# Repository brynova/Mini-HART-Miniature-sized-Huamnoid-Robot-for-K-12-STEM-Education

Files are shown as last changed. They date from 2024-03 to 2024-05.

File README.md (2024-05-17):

# Mini-HART 
The goal of this project is to create an affordable humanoid robot that will be used as an educational tool in the classroom. This humanoid can teach 9-12th grade students several aspects of STEM through its creation and use. These aspects consist of items such as 3-D modeling, design, motor control/mechanics, kinematics, programming, and other related STEM topics. This tool is to be provided to institutions in the form of a kit, which will consist of all necessary mechanical parts and 3-D printed part files. If the institution does not have access to a 3-D printer, the kit can also provide these 3-D printed parts. There will also be instructions to build and program the robot that can be understood/created by someone with limited to no prior knowledge.

Design Process: For the lower body, there were multiple iterations of the lower body connection pieces. In the beginning, the parts were made too thin. This would cause snapping when the robot is in use. To prevent this, the part was made thicker. This was changed with the failure mode in mind. Due to the possible snapping or breakage, this could cause injury to the user. This can be caused by the part being roughly used or even accidents. The reccomended action to prevent this would be a thicker infill. Fillets were also added as a saftey precaution. Sharp edges can add injury if the user is not careful.

## 3-D MODELS:
The 3D models are separted between two parts being the upper body and lower body motor sections in the "Arm Parts" and "LEG Parts" 
folders with the most recent files made for project.Going into the STL within GitHub also provides a visual of what the STL file 
looks like when selected as an added feature for their vizualization.

*** _Arm_Parts_Folder:_ ***

**Arm.STL** - this is the link which connects the shoulder roll directional motor to the hand motor. 

**Hand.STL** - is the model for hand appendage of the robot which is also connected by the last roll 
directional motor of the arm's hand movement. 

**Shoulder.STL** - as this connection is responsible for connecting the arm of the robot to the torso, for this piece the 
motor attached to the torso is facing in the pitch direction axis. 
The placement of each of these motors are also visualized in the "Mini-HART" manual as well for the robots full set up.

***LEG PARTS Folder:***
In the "LEG PARTS" folder it consists of eight files with four of them starting with the labels "LL" and "UL" which stand for 
the "Upper leg" and "lower leg" of the robot. Along with the titles "Back" and "Front" for the placement 
of the part as "Back" refers to the inner placement of the robots leg, and "Front" for the outter placement of the part.

**LL Back.STL** -
This lower leg back part is responsible for the link between the knee 
    
**LL Front.STL** - 
    
**Left Foot.STL** - 
   
**Right Foot.STL** - 
    
**Roll.STL** -
    
**UL BACK.STL** - 
    
**UL Front.STL** - 
    
**Yaw.STL** - 

## Arduino Code

**Commander.ino** -

**Do.a.split** - 

**Kiwon_Squat_perfected** - 

**LegRaise** -

**Leg_Raise(Right)** -

**Movement_Communication** -

**StationarywalkV2** -

**XL-320move.ino** - 

## Blender Simulation

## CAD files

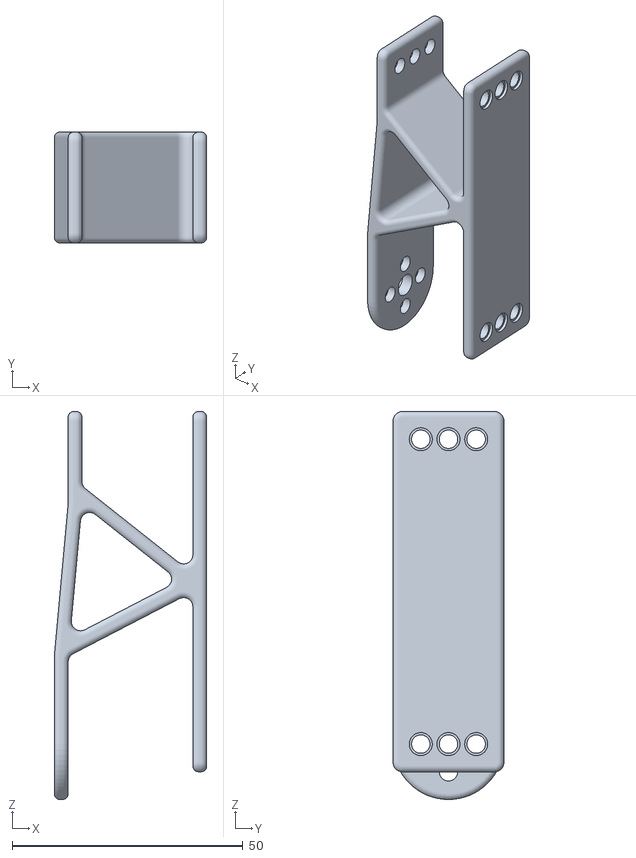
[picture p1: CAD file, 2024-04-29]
3-D Models/Arm Parts/Arm.stl
33.0 x 24.0 x 84.0

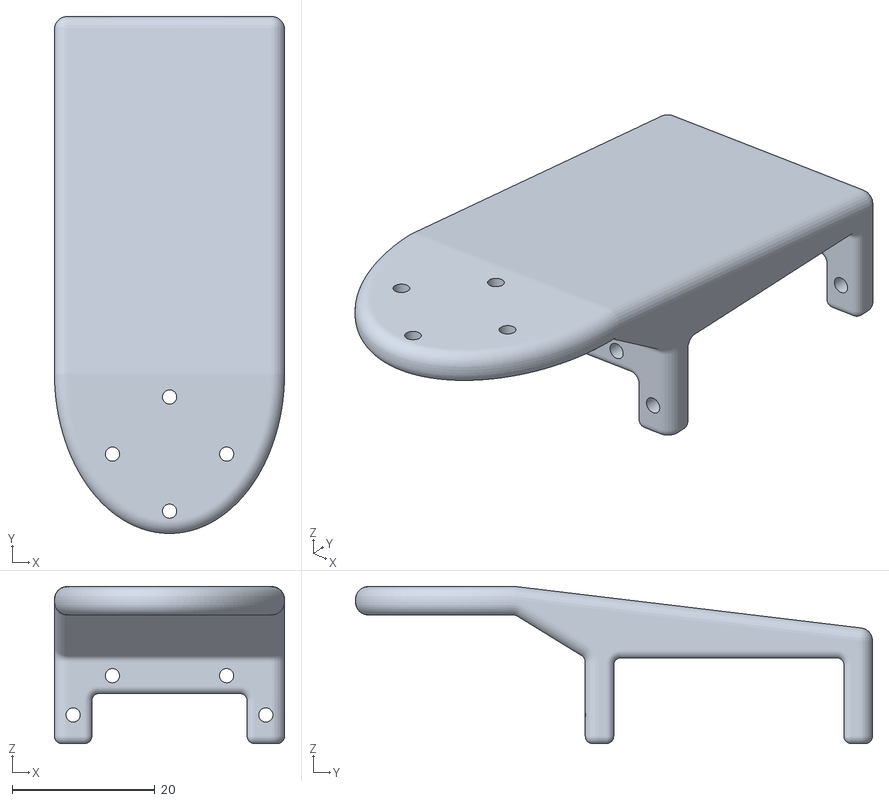
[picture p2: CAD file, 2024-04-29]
3-D Models/LEG PARTS/Yaw.stl
32.2 x 72.4 x 22.0

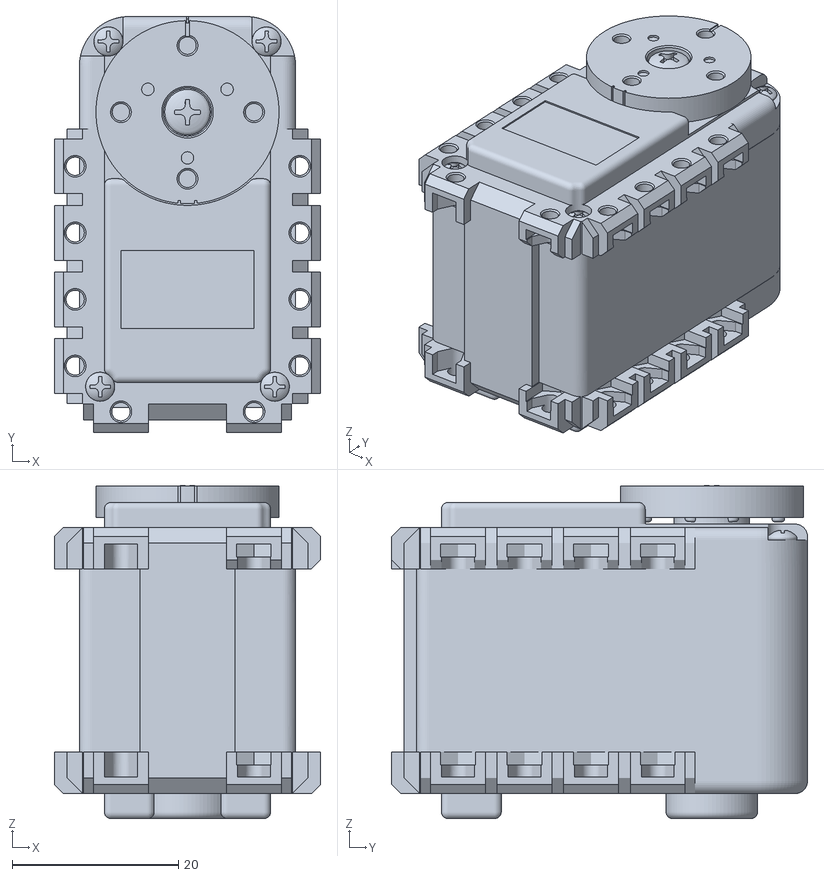
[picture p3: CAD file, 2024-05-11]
Simulink Files/AX-12A Motor v1.stl
32.0 x 50.0 x 40.0

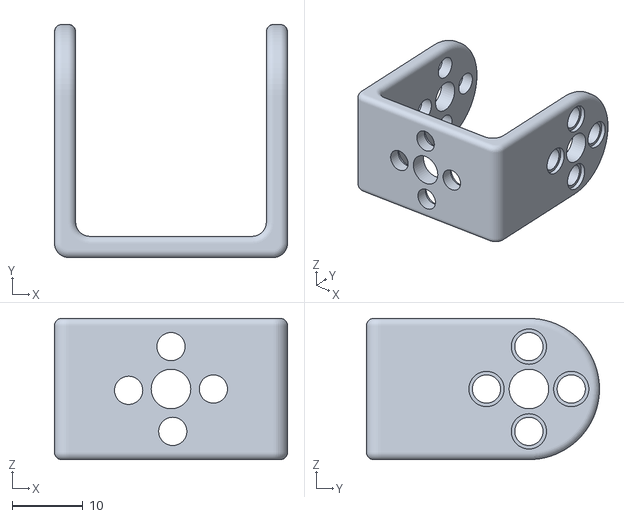
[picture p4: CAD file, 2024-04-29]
3-D Models/Arm Parts/Shoulder.stl
33.0 x 33.0 x 20.0

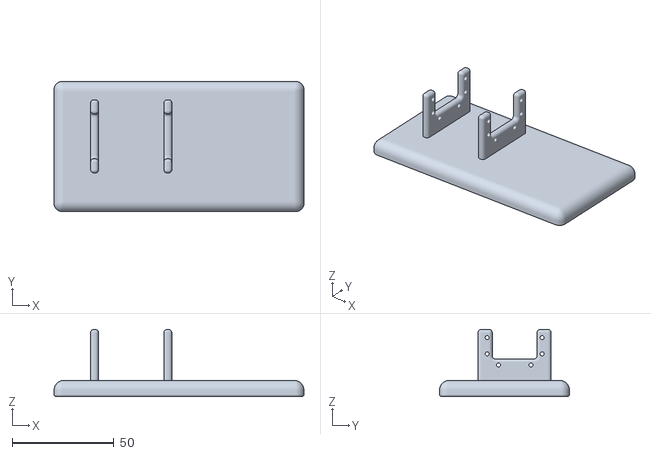
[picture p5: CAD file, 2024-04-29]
3-D Models/LEG PARTS/Right Foot.stl
123.0 x 64.0 x 33.0

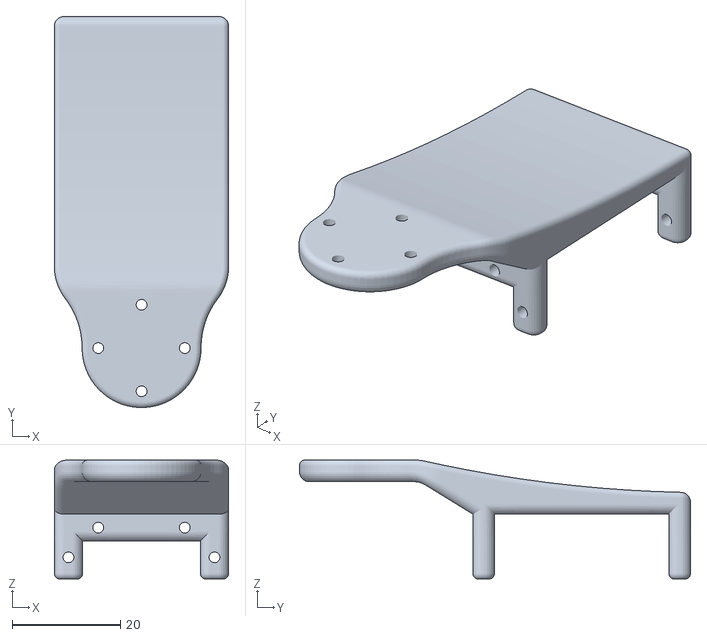
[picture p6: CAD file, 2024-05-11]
Simulink Files/yaw_body_updated_v1.stl
32.2 x 72.3 x 22.0

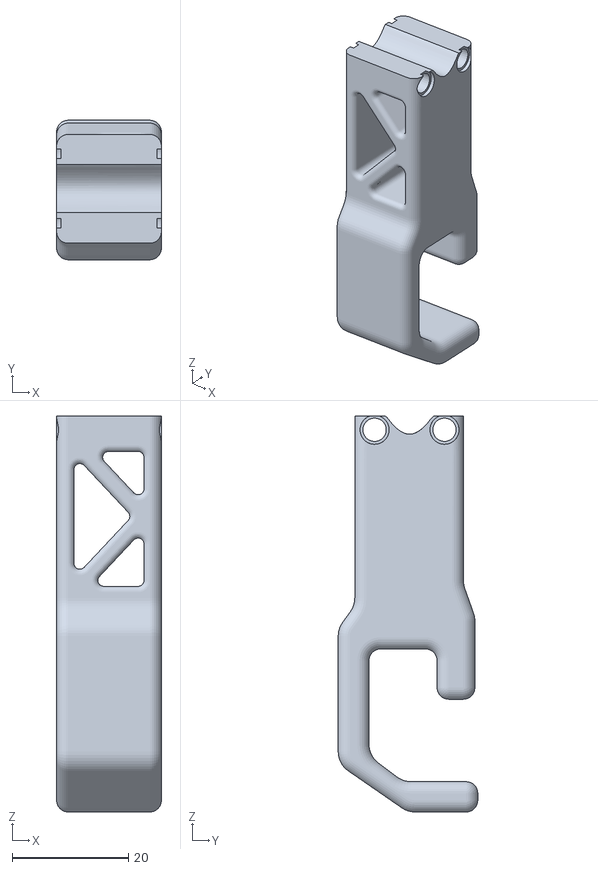
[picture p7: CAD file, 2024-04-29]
3-D Models/Arm Parts/Hand.stl
18.0 x 24.0 x 68.0

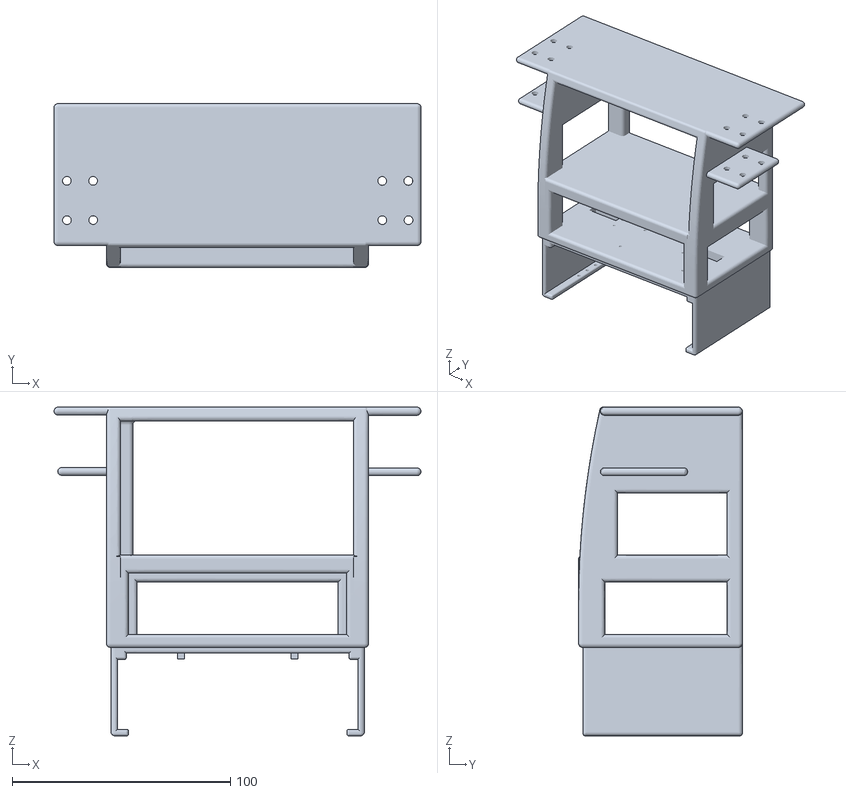
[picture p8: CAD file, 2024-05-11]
Simulink Files/Torso v4.stl
168.0 x 75.0 x 150.5

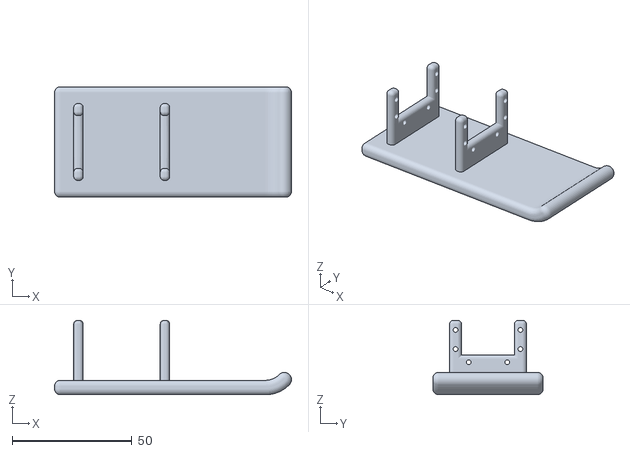
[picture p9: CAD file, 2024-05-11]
Simulink Files/Leg_Parts_foot_v1.stl
98.8 x 46.0 x 31.0

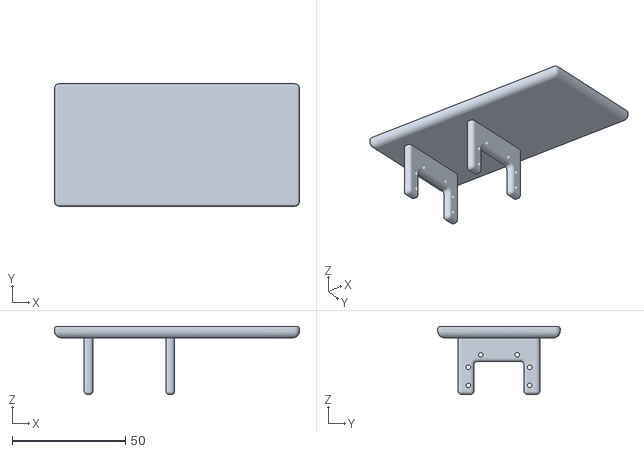
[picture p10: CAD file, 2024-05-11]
Simulink Files/hip_diagram_FootV2_v1.stl
108.0 x 54.0 x 30.0

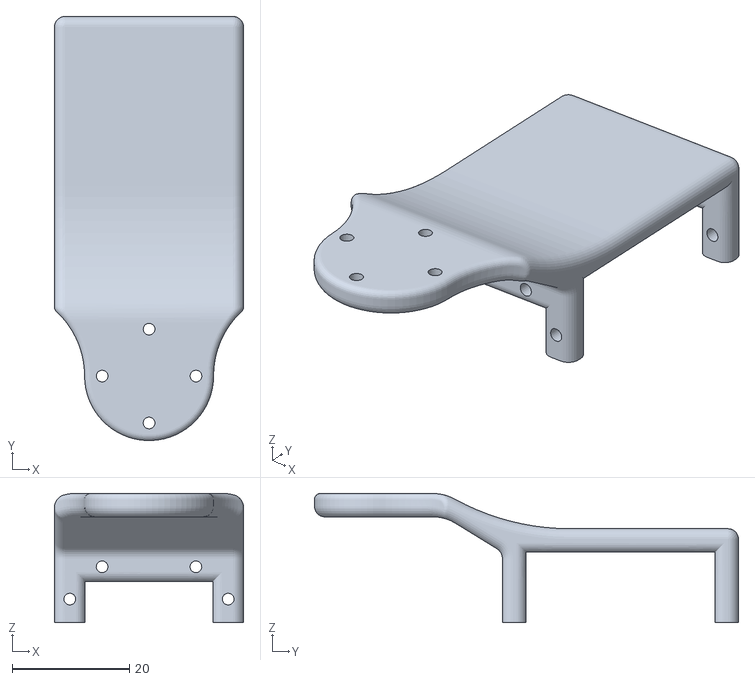
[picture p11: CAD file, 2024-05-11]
Simulink Files/Leg_Parts_Hip_Yaw_v1.stl
32.2 x 72.3 x 22.0

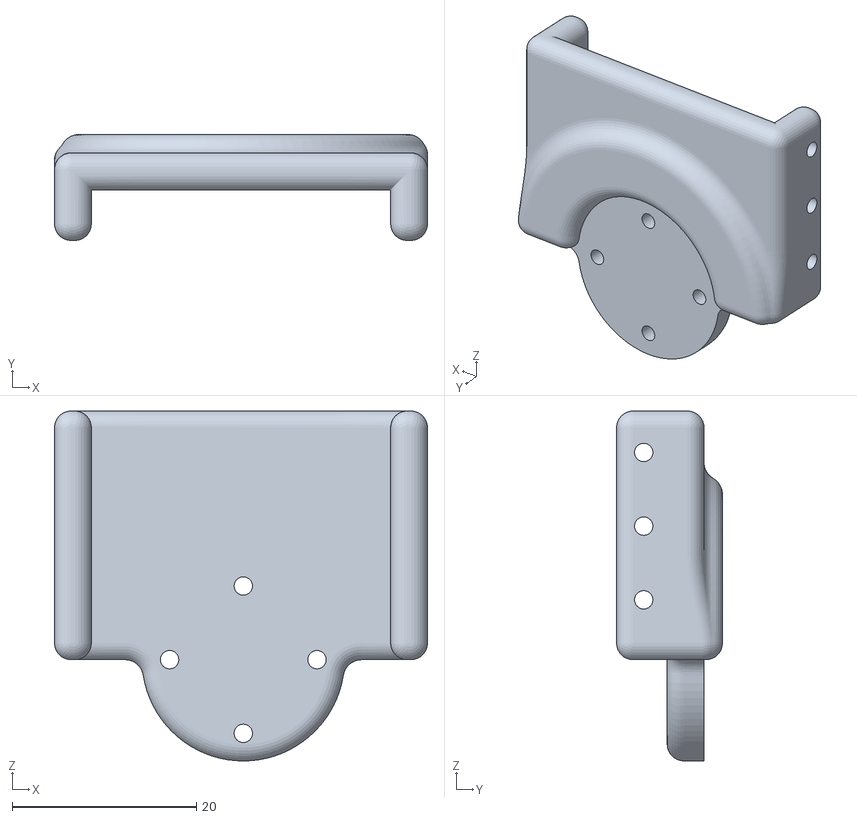
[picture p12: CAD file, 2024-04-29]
Simulink Files/Leg_Parts_roll_v1.stl
40.5 x 11.5 x 38.0

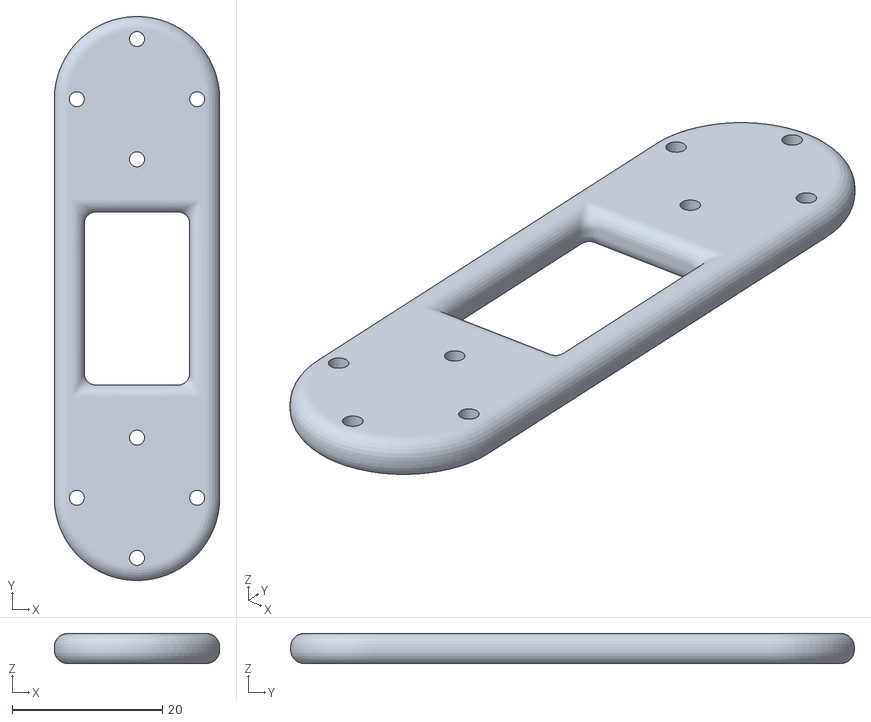
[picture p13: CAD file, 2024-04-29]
Simulink Files/Leg_Parts_LL_Front_v1.stl
22.0 x 75.0 x 4.00

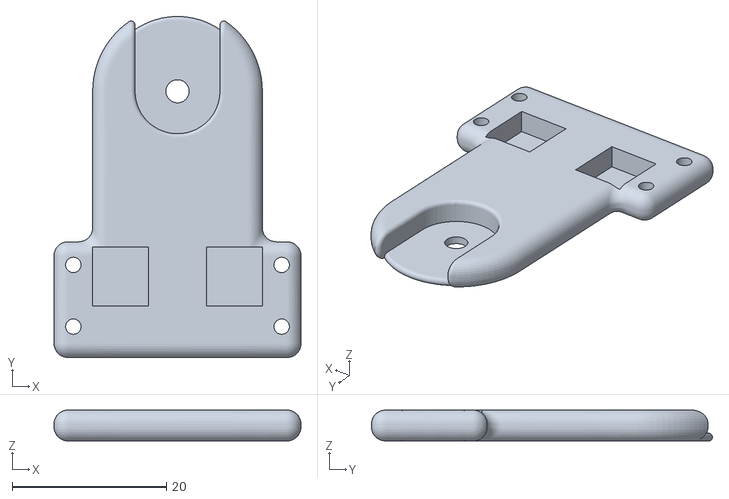
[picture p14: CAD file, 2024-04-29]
Simulink Files/Leg_Parts_UL_Back_v1.stl
32.0 x 44.2 x 4.00

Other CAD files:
3-D Models/LEG PARTS/Left Foot.stl
Simulink Files/Leg_Parts_UL_Front_v2.stl
Simulink Files/Leg_Parts_LL_Back_v1.stl

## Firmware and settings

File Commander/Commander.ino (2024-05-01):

#include <DynamixelSDK.h>

//Define Settings for AX motors
#define ADDR_AX_TORQUE_ENABLE          24
#define ADDR_AX_GOAL_POSITION          30
#define ADDR_AX_MOVING_SPEED           32
#define ADDR_AX_PRESENT_POSITION       36  
#define PROTOCOL_VERSION               1.0
#define BAUDRATE                       1000000
#define DEVICENAME                     "3"

//Define Settings for XL motors
#define ADDR_XL_TORQUE_ENABLE          24
#define ADDR_XL_GOAL_POSITION          30
#define ADDR_XL_MOVING_SPEED           32  
#define ADDR_XL_PRESENT_POSITION       37
#define PROTOCOL_VERSION_XL            2.0
#define BAUDRATE_XL                    1000000
#define DEVICENAME_XL                  "1"

#define GenSpeed                       700

String in;

//Porting AX motors
dynamixel::PortHandler *portHandler;
dynamixel::PacketHandler *packetHandler;
uint8_t dxl_error = 0; // Variable to hold Dynamixel error codes
int dxl_comm_result = COMM_TX_FAIL; // Variable to hold the result of Dynamixel communication operations

//Porting XL motors
dynamixel::PortHandler *portHandler_XL;
dynamixel::PacketHandler *packetHandler_XL;
uint8_t dxl_error_XL = 0;
int dxl_comm_result_XL = COMM_TX_FAIL;


void enableTorque(int id);
void disableTorque(int id);
void setMovingSpeed(int id, int speed);
void moveMotor(int id, float angle, int time);
int angleToPosition(float angle, int id);
int getCurrentPosition(int id); // Function to read the current position of a motor

void enableTorque_XL(int id);
void disableTorque_XL(int id);
void setMovingSpeed_XL(int id, int speed);
void moveMotor_XL(int id, float angle, int time);
int angleToPosition_XL(float angle, int id);
int getCurrentPosition_XL(int id);

void setup() {
    Serial.begin(57600);
    portHandler = dynamixel::PortHandler::getPortHandler(DEVICENAME);
    packetHandler = dynamixel::PacketHandler::getPacketHandler(PROTOCOL_VERSION);

    if (!portHandler->openPort() || !portHandler->setBaudRate(BAUDRATE)) {
        Serial.println("Failed to open port or set baud rate");
        return;
    }

    portHandler_XL = dynamixel::PortHandler::getPortHandler(DEVICENAME_XL);
    packetHandler_XL = dynamixel::PacketHandler::getPacketHandler(PROTOCOL_VERSION_XL);

    if (!portHandler_XL->openPort() || !portHandler_XL->setBaudRate(BAUDRATE_XL)) {
        Serial.println("Failed to open port or set baud rate");
        return;
    }

    for (int id = 1; id <= 12; id++) {
        enableTorque(id);
        moveMotor(id, 0, 200); // Initialize motors to stand position
    }
    delay(200);

    for (int id = 13; id <= 18; id++) {
        enableTorque_XL(id);
        moveMotor_XL(id, 0, 200);
    }
    delay(1000);


  
}


void loop() {
    if (Serial.available() > 0) { // Check if data is available to read
        in = Serial.readStringUntil('\n'); // Read the string until a newline character

        // Remove any whitespace or non-printable characters that might affect string comparison
        in.trim();

        // Process the command
        if (in == "Wave") {
            // Execute wave sequence
            wave();
        } else if (in == "Bow") {
            // Execute bow sequence
            bow();
        } else if (in == "Squat") {
            // Execute bow sequence
            squat();
        } else if (in == "Split") {
            // Execute bow sequence
            split();
        } else if (in == "Balance") {
            // Execute bow sequence
            balance();
        } else if (in == "Walk") {
            walk();
        }

        in = "";
    }

    // Delay slightly to prevent overloading the serial buffer with continuous commands
    delay(500);
    
    // Prompt user for input, only if there is no pending data in the buffer
    if (!Serial.available()) {
        Serial.println("Enter movement command:");
    }
}


//////////////////////////////////Start of Void Commands for AX//////////////////////////////////


void enableTorque(int id) {
    packetHandler->write1ByteTxRx(portHandler, id, ADDR_AX_TORQUE_ENABLE, 1, &dxl_error);
}

void disableTorque(int id) {
    packetHandler->write1ByteTxRx(portHandler, id, ADDR_AX_TORQUE_ENABLE, 0, &dxl_error);
}

void setMovingSpeed(int id, int speed) {
    dxl_comm_result = packetHandler->write2ByteTxRx(portHandler, id, ADDR_AX_MOVING_SPEED, speed, &dxl_error);
    if (dxl_comm_result != COMM_SUCCESS) {
        Serial.println("Failed to set moving speed!");
    }
}

void moveMotor(int id, float angle, int time) {
    // Adjust angle for motors for robotics coding needs
    if (id >= 11 && id <= 12) {
        angle *= -1;
    }
    if (id >= 1 && id <= 1) {
        angle *= -1;
    }
    if (id >= 6 && id <= 7) {
        angle *= -1;
    }
    if (id >= 3 && id <= 4) {
        angle *= -1;
    }
    
    // Get current and goal positions
    int currentPosition = getCurrentPosition(id);
    int goalPosition = angleToPosition(angle, id);

    // Calculate and set speed if time is valid
    if (time > 0) {
        int movementMagnitude = abs(goalPosition - currentPosition);
        int speed = (movementMagnitude * 1000 / time) / 2.286;
        
        // Manually constrain the speed to be non-negative and no greater than 1023
        if(speed < 0){
            speed = -speed;  // Make speed positive if negative
        }
        if(speed > 1023){
            speed = 1023;  // Constrain speed to a maximum of 1023
        }

        setMovingSpeed(id, speed); // Set motor speed
    }

    // Move motor to goal position
    packetHandler->write2ByteTxRx(portHandler, id, ADDR_AX_GOAL_POSITION, goalPosition, &dxl_error);
    if (dxl_comm_result != COMM_SUCCESS) {
        Serial.println("Failed to move motor!");
    }
}


int angleToPosition(float angle, int id) {
    return (int)(((angle + 150) / 300) * 1023);
}

// Function to read the current position of a motor
int getCurrentPosition(int id) {
    uint16_t dxl_present_position;
    dxl_comm_result = packetHandler->read2ByteTxRx(portHandler, id, ADDR_AX_PRESENT_POSITION, &dxl_present_position, &dxl_error);
    if (dxl_comm_result == COMM_SUCCESS) {
        return dxl_present_position;
    } else {
        Serial.println("Failed to read present position!");
        return -1; // Handle error appropriately
    }
}

//////////////////////////////////Start of Void Commands for XL//////////////////////////////////


void enableTorque_XL(int id) {
    packetHandler_XL->write1ByteTxRx(portHandler_XL, id, ADDR_XL_TORQUE_ENABLE, 1, &dxl_error_XL);
}

void disableTorque_XL(int id) {
    packetHandler_XL->write1ByteTxRx(portHandler_XL, id, ADDR_XL_TORQUE_ENABLE, 0, &dxl_error_XL);
}

void setMovingSpeed_XL(int id, int speed) {
    dxl_comm_result_XL = packetHandler_XL->write2ByteTxRx(portHandler_XL, id, ADDR_XL_MOVING_SPEED, speed, &dxl_error_XL);
    if (dxl_comm_result_XL != COMM_SUCCESS) {
        Serial.println("Failed to set moving speed!");
    }
}

void moveMotor_XL(int id, float angle, int time) {
    if (id >= 13 && id <= 15) {
        angle *= -1;
    }
    if (id >= 17 && id <= 18) {
        angle *= -1;
    }
    

    int currentPosition_XL = getCurrentPosition_XL(id);
    int goalPosition_XL = angleToPosition_XL(angle, id);

    if (time > 0) {
        int movementMagnitude_XL = abs(goalPosition_XL - currentPosition_XL);
        int speed_XL = (movementMagnitude_XL * 1000 / time) / 2.286;
        
        // Manually constrain the speed to be non-negative and no greater than 1023
        if(speed_XL < 0){
            speed_XL = -speed_XL;  // Make speed positive if negative
        }
        if(speed_XL > 1023){
            speed_XL = 1023;  // Constrain speed to a maximum of 1023
        }

        setMovingSpeed_XL(id, speed_XL);
    }

    packetHandler_XL->write2ByteTxRx(portHandler_XL, id, ADDR_XL_GOAL_POSITION, goalPosition_XL, &dxl_error_XL);
    if (dxl_comm_result_XL != COMM_SUCCESS) {
        Serial.println("Failed to move motor!");
    }
}

int angleToPosition_XL(float angle, int id) {
    return (int)(((angle + 150) / 300) * 1023);
}

int getCurrentPosition_XL(int id) {
    uint16_t dxl_present_position_XL;
    dxl_comm_result_XL = packetHandler_XL->read2ByteTxRx(portHandler_XL, id, ADDR_XL_PRESENT_POSITION, &dxl_present_position_XL, &dxl_error_XL);
    if (dxl_comm_result_XL == COMM_SUCCESS) {
        return dxl_present_position_XL;
    } else {
        Serial.println("Failed to read present position!");
        return -1;
    }
}

//////////////////////////////////Start of Preset Movement Commands//////////////////////////////////

void end(){
  for (int id = 1; id <= 12; id++) {
        enableTorque(id);
        moveMotor(id, 0, 200);
    }
    delay(200);

    for (int id = 13; id <= 18; id++) {
        enableTorque_XL(id);
        moveMotor_XL(id, 0, 200);
    }
    delay(1000);
}

void wave(){
    moveMotor_XL(  13, -150, 400); // SR Right
    moveMotor_XL(  14,    0, 400); // SP Right
    moveMotor_XL(  15,    0, 400); // FP Right

    moveMotor_XL(  16,    0, 400); // SR Left
    moveMotor_XL(  17,    0, 400); // SP Left
    moveMotor_XL(  18,    0, 400); // FP Left

    delay(500);

    moveMotor_XL(  13, -150, 300); // SR Right
    moveMotor_XL(  14,   10, 300); // SP Right
    moveMotor_XL(  15,   40, 300); // FP Right

    moveMotor_XL(  16,    0, 300); // SR Left
    moveMotor_XL(  17,    0, 300); // SP Left
    moveMotor_XL(  18,    0, 300); // FP Left

    delay(400);

    moveMotor_XL(  13, -150, 300); // SR Right
    moveMotor_XL(  14,   10, 300); // SP Right
    moveMotor_XL(  15,  -40, 300); // FP Right

    moveMotor_XL(  16,    0, 300); // SR Left
    moveMotor_XL(  17,    0, 300); // SP Left
    moveMotor_XL(  18,    0, 300); // FP Left

    delay(400);

    moveMotor_XL(  13, -150, 300); // SR Right
    moveMotor_XL(  14,   10, 300); // SP Right
    moveMotor_XL(  15,   40, 300); // FP Right

    moveMotor_XL(  16,    0, 300); // SR Left
    moveMotor_XL(  17,    0, 300); // SP Left
    moveMotor_XL(  18,    0, 300); // FP Left

    delay(400);

    moveMotor_XL(  13, -150, 300); // SR Right
    moveMotor_XL(  14,   10, 300); // SP Right
    moveMotor_XL(  15,  -40, 300); // FP Right

    moveMotor_XL(  16,    0, 300); // SR Left
    moveMotor_XL(  17,    0, 300); // SP Left
    moveMotor_XL(  18,    0, 300); // FP Left

    delay(400);

//other arm

    moveMotor_XL(  13,    0, 400); // SR Right
    moveMotor_XL(  14,    0, 400); // SP Right
    moveMotor_XL(  15,    0, 400); // FP Right

    moveMotor_XL(  16, -150, 400); // SR Left
    moveMotor_XL(  17,    0, 400); // SP Left
    moveMotor_XL(  18,    0, 400); // FP Left

    delay(500);

    moveMotor_XL(  13,    0, 300); // SR Right
    moveMotor_XL(  14,    0, 300); // SP Right
    moveMotor_XL(  15,    0, 300); // FP Right

    moveMotor_XL(  16, -150, 300); // SR Left
    moveMotor_XL(  17,   10, 300); // SP Left
    moveMotor_XL(  18,  -40, 300); // FP Left

    delay(400);

    moveMotor_XL(  13,    0, 300); // SR Right
    moveMotor_XL(  14,    0, 300); // SP Right
    moveMotor_XL(  15,    0, 300); // FP Right

    moveMotor_XL(  16, -150, 300); // SR Left
    moveMotor_XL(  17,   10, 300); // SP Left
    moveMotor_XL(  18,   40, 300); // FP Left

    delay(400);

    moveMotor_XL(  13,    0, 300); // SR Right
    moveMotor_XL(  14,    0, 300); // SP Right
    moveMotor_XL(  15,    0, 300); // FP Right

    moveMotor_XL(  16, -150, 300); // SR Left
    moveMotor_XL(  17,   10, 300); // SP Left
    moveMotor_XL(  18,  -40, 300); // FP Left

    delay(400);

    moveMotor_XL(  13,    0, 300); // SR Right
    moveMotor_XL(  14,    0, 300); // SP Right
    moveMotor_XL(  15,    0, 300); // FP Right

    moveMotor_XL(  16, -150, 300); // SR Left
    moveMotor_XL(  17,   10, 300); // SP Left
    moveMotor_XL(  18,   40, 300); // FP Left

    delay(400);

//Both Arms
    moveMotor_XL(  13, -150, 400); // SR Right
    moveMotor_XL(  14,    0, 400); // SP Right
    moveMotor_XL(  15,    0, 400); // FP Right

    moveMotor_XL(  16, -150, 400); // SR Left
    moveMotor_XL(  17,    0, 400); // SP Left
    moveMotor_XL(  18,    0, 400); // FP Left

    delay(500);

    moveMotor_XL(  13, -150, 300); // SR Right
    moveMotor_XL(  14,   10, 300); // SP Right
    moveMotor_XL(  15,   40, 300); // FP Right

    moveMotor_XL(  16, -150, 300); // SR Left
    moveMotor_XL(  17,   10, 300); // SP Left
    moveMotor_XL(  18,  -40, 300); // FP Left

    delay(400);

    moveMotor_XL(  13, -150, 300); // SR Right
    moveMotor_XL(  14,   10, 300); // SP Right
    moveMotor_XL(  15,  -40, 300); // FP Right

    moveMotor_XL(  16, -150, 300); // SR Left
    moveMotor_XL(  17,   10, 300); // SP Left
    moveMotor_XL(  18,   40, 300); // FP Left

    delay(400);

    moveMotor_XL(  13, -150, 300); // SR Right
    moveMotor_XL(  14,   10, 300); // SP Right
    moveMotor_XL(  15,   40, 300); // FP Right

    moveMotor_XL(  16, -150, 300); // SR Left
    moveMotor_XL(  17,   10, 300); // SP Left
    moveMotor_XL(  18,  -40, 300); // FP Left

    delay(400);

    moveMotor_XL(  13, -150, 300); // SR Right
    moveMotor_XL(  14,   10, 300); // SP Right
    moveMotor_XL(  15,  -40, 300); // FP Right

    moveMotor_XL(  16, -150, 300); // SR Left
    moveMotor_XL(  17,   10, 300); // SP Left
    moveMotor_XL(  18,   40, 300); // FP Left

    delay(400);

    end();
    delay(1000);

}

void bow(){
    moveMotor(  1,     0, 400); // HY Right
    moveMotor(  2,     0, 400); // HR Right
    moveMotor(  3,   -80, 400); // HP Right
    moveMotor(  4,    60, 400); // KP Right
    moveMotor(  5,     0, 400); // AP Right
    moveMotor(  6,     0, 400); // AR Right

    moveMotor(  7,     0, 400); // HY Left
    moveMotor(  8,     0, 400); // HR Left 
    moveMotor(  9,   -80, 400); // HP Left
    moveMotor( 10,    60, 400); // KP Left
    moveMotor( 11,     0, 400); // AP Left
    moveMotor( 12,     0, 400); // AR Left

    moveMotor_XL(  13,  -45, 400); // SR Right
    moveMotor_XL(  14,    0, 400); // SP Right
    moveMotor_XL(  15,    0, 400); // FP Right

    moveMotor_XL(  16,   45, 400); // SR Left
    moveMotor_XL(  17,    0, 400); // SP Left
    moveMotor_XL(  18,    0, 400); // FP Left

    delay(500);

    moveMotor(  1,     0, 400); // HY Right
    moveMotor(  2,     0, 400); // HR Right
    moveMotor(  3,   -80, 400); // HP Right
    moveMotor(  4,    60, 400); // KP Right
    moveMotor(  5,     0, 400); // AP Right
    moveMotor(  6,     0, 400); // AR Right

    moveMotor(  7,     0, 400); // HY Left
    moveMotor(  8,     0, 400); // HR Left 
    moveMotor(  9,   -80, 400); // HP Left
    moveMotor( 10,    60, 400); // KP Left
    moveMotor( 11,     0, 400); // AP Left
    moveMotor( 12,     0, 400); // AR Left

    moveMotor_XL(  13,  -45, 400); // SR Right
    moveMotor_XL(  14,    0, 400); // SP Right
    moveMotor_XL(  15,   90, 400); // FP Right

    moveMotor_XL(  16,   45, 400); // SR Left
    moveMotor_XL(  17,    0, 400); // SP Left
    moveMotor_XL(  18,   -90, 400); // FP Left

    delay(1000);

    moveMotor(  1,     0, 400); // HY Right
    moveMotor(  2,     0, 400); // HR Right
    moveMotor(  3,   -80, 400); // HP Right
    moveMotor(  4,    60, 400); // KP Right
    moveMotor(  5,     0, 400); // AP Right
    moveMotor(  6,     0, 400); // AR Right

    moveMotor(  7,     0, 400); // HY Left
    moveMotor(  8,     0, 400); // HR Left 
    moveMotor(  9,   -80, 400); // HP Left
    moveMotor( 10,    60, 400); // KP Left
    moveMotor( 11,     0, 400); // AP Left
    moveMotor( 12,     0, 400); // AR Left

    moveMotor_XL(  13,  -45, 400); // SR Right
    moveMotor_XL(  14,    0, 400); // SP Right
    moveMotor_XL(  15,    0, 400); // FP Right

    moveMotor_XL(  16,   45, 400); // SR Left
    moveMotor_XL(  17,    0, 400); // SP Left
    moveMotor_XL(  18,    0, 400); // FP Left

    delay(500);

    moveMotor(  1,     0, 400); // HY Right
    moveMotor(  2,     0, 400); // HR Right
    moveMotor(  3,   -80, 400); // HP Right
    moveMotor(  4,    60, 400); // KP Right
    moveMotor(  5,     0, 400); // AP Right
    moveMotor(  6,     0, 400); // AR Right

    moveMotor(  7,     0, 400); // HY Left
    moveMotor(  8,     0, 400); // HR Left 
    moveMotor(  9,   -80, 400); // HP Left
    moveMotor( 10,    60, 400); // KP Left
    moveMotor( 11,     0, 400); // AP Left
    moveMotor( 12,     0, 400); // AR Left

    moveMotor_XL(  13,   45, 400); // SR Right
    moveMotor_XL(  14,    0, 400); // SP Right
    moveMotor_XL(  15,    0, 400); // FP Right

    moveMotor_XL(  16,  -45, 400); // SR Left
    moveMotor_XL(  17,    0, 400); // SP Left
    moveMotor_XL(  18,    0, 400); // FP Left

    delay(100);


    moveMotor(  1,     0, 400); // HY Right
    moveMotor(  2,     0, 400); // HR Right
    moveMotor(  3,   -80, 400); // HP Right
    moveMotor(  4,    60, 400); // KP Right
    moveMotor(  5,     0, 400); // AP Right
    moveMotor(  6,     0, 400); // AR Right

    moveMotor(  7,     0, 400); // HY Left
    moveMotor(  8,     0, 400); // HR Left 
    moveMotor(  9,   -80, 400); // HP Left
    moveMotor( 10,    60, 400); // KP Left
    moveMotor( 11,     0, 400); // AP Left
    moveMotor( 12,     0, 400); // AR Left

    moveMotor_XL(  13,   45, 400); // SR Right
    moveMotor_XL(  14,    0, 400); // SP Right
    moveMotor_XL(  15,   90, 400); // FP Right

    moveMotor_XL(  16,  -45, 400); // SR Left
    moveMotor_XL(  17,    0, 400); // SP Left
    moveMotor_XL(  18,  -90, 400); // FP Left

    delay(1000);


    moveMotor(  1,     0, 400); // HY Right
    moveMotor(  2,     0, 400); // HR Right
    moveMotor(  3,   -80, 400); // HP Right
    moveMotor(  4,    60, 400); // KP Right
    moveMotor(  5,     0, 400); // AP Right
    moveMotor(  6,     0, 400); // AR Right

    moveMotor(  7,     0, 400); // HY Left
    moveMotor(  8,     0, 400); // HR Left 
    moveMotor(  9,   -80, 400); // HP Left
    moveMotor( 10,    60, 400); // KP Left
    moveMotor( 11,     0, 400); // AP Left
    moveMotor( 12,     0, 400); // AR Left

    moveMotor_XL(  13,   45, 400); // SR Right
    moveMotor_XL(  14,    0, 400); // SP Right
    moveMotor_XL(  15,    0, 400); // FP Right

    moveMotor_XL(  16,  -45, 400); // SR Left
    moveMotor_XL(  17,    0, 400); // SP Left
    moveMotor_XL(  18,    0, 400); // FP Left

    delay(500);

    end();
    delay(2000);
}
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

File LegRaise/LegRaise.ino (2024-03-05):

#include <DynamixelSDK.h>

// Control table addresses
#define ADDR_AX_TORQUE_ENABLE          24
#define ADDR_AX_GOAL_POSITION          30
#define ADDR_AX_PRESENT_POSITION       36

// Protocol version
#define PROTOCOL_VERSION               1.0

// Default settings
#define DXL_ID_1                       3    // ID of the first motor
#define DXL_ID_2                       4    // ID of the second motor
#define DXL_ID_3                       5    // ID of the third motor
#define DXL_ID_4                       6    // ID of the fourth motor
#define DXL_ID_5                       7    // ID of the fith motor
#define DXL_ID_6                       8    // ID of the sixth motor

#define BAUDRATE                       1000000
#define DEVICENAME                     "3"  // Use Serial3 for OpenCM 485 EXP
#define TORQUE_ENABLE                  1
#define TORQUE_DISABLE                 0
// Updated to use angle for initial and goal positions
//#define DXL_INITIAL_ANGLE              150 // Initial angle
//#define DXL_GOAL_ANGLE                 240  // New target angle for both motors

dynamixel::PortHandler *portHandler;
dynamixel::PacketHandler *packetHandler;

// Function to convert angle to position
int angleToPosition(float angle) {
  return (int)(angle / 300 * 1023);
}

void setup() {
  Serial.begin(115200);
  while(!Serial); // Wait for Serial port to connect

  portHandler = dynamixel::PortHandler::getPortHandler(DEVICENAME);
  packetHandler = dynamixel::PacketHandler::getPacketHandler(PROTOCOL_VERSION);

  // Open port
  if (!portHandler->openPort()) {
    Serial.println("Failed to open the port!");
    return;
  }

  // Set port baudrate
  if (!portHandler->setBaudRate(BAUDRATE)) {
    Serial.println("Failed to set the baudrate!");
    return;
  }

  // Enable Dynamixel Torque for both motors
  uint8_t dxl_error = 0;
  int dxl_comm_result = COMM_TX_FAIL;

  // Enable torque for both motors
  enableTorque(DXL_ID_1, dxl_error, dxl_comm_result);
  enableTorque(DXL_ID_2, dxl_error, dxl_comm_result);
  enableTorque(DXL_ID_3, dxl_error, dxl_comm_result);
  enableTorque(DXL_ID_4, dxl_error, dxl_comm_result);
  enableTorque(DXL_ID_5, dxl_error, dxl_comm_result);
  enableTorque(DXL_ID_6, dxl_error, dxl_comm_result);

  // Convert angles to positions and move motors
  moveMotor(DXL_ID_1, angleToPosition(150), dxl_error, dxl_comm_result);
  moveMotor(DXL_ID_2, angleToPosition(150), dxl_error, dxl_comm_result);
  moveMotor(DXL_ID_3, angleToPosition(150), dxl_error, dxl_comm_result);
  moveMotor(DXL_ID_4, angleToPosition(150), dxl_error, dxl_comm_result);
  moveMotor(DXL_ID_5, angleToPosition(150), dxl_error, dxl_comm_result);
  moveMotor(DXL_ID_6, angleToPosition(150), dxl_error, dxl_comm_result);
  delay(2000); // Wait for motors to reach the initial position

  // Move both motors to new goal position
  moveMotor(DXL_ID_1, angleToPosition(240), dxl_error, dxl_comm_result);
  moveMotor(DXL_ID_2, angleToPosition(60), dxl_error, dxl_comm_result);
  moveMotor(DXL_ID_3, angleToPosition(60), dxl_error, dxl_comm_result);//need to modify the angle
  moveMotor(DXL_ID_4, angleToPosition(60), dxl_error, dxl_comm_result);//need to modify the angle
  moveMotor(DXL_ID_5, angleToPosition(60), dxl_error, dxl_comm_result);//need to modify the angle
  moveMotor(DXL_ID_6, angleToPosition(60), dxl_error, dxl_comm_result);//need to modify the angle
  delay(2000); // Wait for motors to reach the new goal position

  // Move both motors back to the initial angle
  moveMotor(DXL_ID_1, angleToPosition(150), dxl_error, dxl_comm_result);
  moveMotor(DXL_ID_2, angleToPosition(150), dxl_error, dxl_comm_result);
  moveMotor(DXL_ID_3, angleToPosition(150), dxl_error, dxl_comm_result);
  moveMotor(DXL_ID_4, angleToPosition(150), dxl_error, dxl_comm_result);
  moveMotor(DXL_ID_5, angleToPosition(150), dxl_error, dxl_comm_result);
  moveMotor(DXL_ID_6, angleToPosition(150), dxl_error, dxl_comm_result);
  delay(2000); // Wait for motors to move back to the initial position

  // Disable Dynamixel Torque for both motors
  disableTorque(DXL_ID_1, dxl_error, dxl_comm_result);
  disableTorque(DXL_ID_2, dxl_error, dxl_comm_result);
  disableTorque(DXL_ID_3, dxl_error, dxl_comm_result);
  disableTorque(DXL_ID_4, dxl_error, dxl_comm_result);
  disableTorque(DXL_ID_5, dxl_error, dxl_comm_result);
  disableTorque(DXL_ID_6, dxl_error, dxl_comm_result);

  // Close port
  portHandler->closePort();
}

void enableTorque(int id, uint8_t &dxl_error, int &dxl_comm_result) {
  dxl_comm_result = packetHandler->write1ByteTxRx(portHandler, id, ADDR_AX_TORQUE_ENABLE, TORQUE_ENABLE, &dxl_error);
  if (dxl_comm_result != COMM_SUCCESS) {
    Serial.println("Failed to enable torque!");
  }
}

void disableTorque(int id, uint8_t &dxl_error, int &dxl_comm_result) {
  dxl_comm_result = packetHandler->write1ByteTxRx(portHandler, id, ADDR_AX_TORQUE_ENABLE, TORQUE_DISABLE, &dxl_error);
  if (dxl_comm_result != COMM_SUCCESS) {
    Serial.println("Failed to disable torque!");
  }
}

void moveMotor(int id, int anglePosition, uint8_t &dxl_error, int &dxl_comm_result) {
  dxl_comm_result = packetHandler->write2ByteTxRx(portHandler, id, ADDR_AX_GOAL_POSITION, anglePosition, &dxl_error);
  if (dxl_comm_result != COMM_SUCCESS) {
    Serial.println("Failed to move motor!");
  }
}

void loop() {
  // Empty loop
}

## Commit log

2024-03-05 Add current arduino files to the repository
2024-04-11 Added the squat Arduino Code for the lower body
2024-04-11 Added the current files for the upper body arms
2024-04-18 Added STL Files for the Lower body in simulation
    [AX-12A Motor v1.stl, Leg_Parts_Hip_Yaw_v1.stl, Leg_Parts_LL_Back_v1.stl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]
2024-04-29 3-D Models for MINI-HART
    [Arm.stl, Hand.stl, LL Back.stl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]
2024-05-01 Code for XL-320 Motors
2024-05-11 Updated instructions for the arm parts of the robot.
